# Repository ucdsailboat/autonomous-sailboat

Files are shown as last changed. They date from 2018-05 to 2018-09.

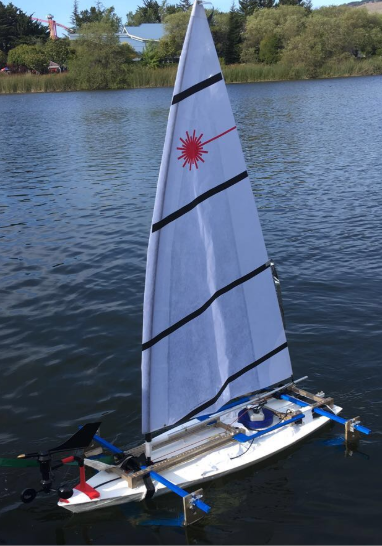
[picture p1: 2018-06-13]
Photos/sailboat.PNG

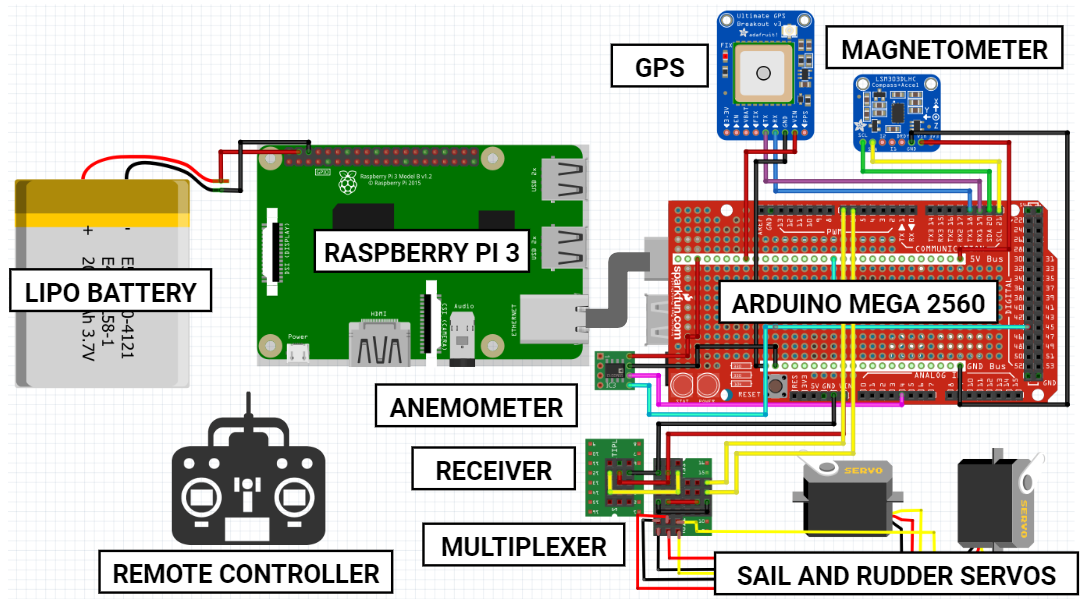
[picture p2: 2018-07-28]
Photos/fritzing sailboat.PNG

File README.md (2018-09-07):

# autonomous-sailboat
This is a repository for the Mechanical Engineering senior design project for UC Davis that focuses on developing an autonomous hydrofoil sailboat.

__Contributors:__ <br/>
Sean Blaevoet, <br/>
Jordan Leung, <br/>
Michele Shi, <br/>
Vivian Tran, <br/>
Bryan Zhao

__Special thanks to:__ <br/>
Davi Henrique & <br/>
University of Southampton Sailing Robot Team (https://github.com/Maritime-Robotics-Student-Society/sailing-robot)

__Robotic Sailboat Wiki at:__ <br/>
https://github.com/ucdsailboat/autonomous-sailboat/wiki

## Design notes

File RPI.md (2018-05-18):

RPI DOCUMENTATION
CONNECTING TO THE RPI WITH WINDOWS REMOTE DESKTOP CONNECTION
If you're setting up the RPI for the first time, you'll need to set it up for remote desktop connection by following this YouTube video and this blog link to fix the default cursor.

Otherwise, to use a laptop's mouse and keyboard, you'll need to connect to the RPi with Window's built-in Remote Desktop Connection (or equivalent on Linux or Mac).

Connect the RPi to the laptop with HDMI
Log into Window's remote desktop connection
COMPUTER: raspberrypi.local
USERNAME: pi
PASSWORD: eme185
DOWNLOADING ARDUINO LIBRARIES ON RPI
Zip folders of the libraries are in the repository.

Download and unzip the folders for the IMU, GPS, and ANEMOMETER. Make sure your .h and .cpp files are not in another folder or else the Arduino IDE won't find the library header.
Move folders to /usr/share/arduino/libraries/ with command terminal and type the following commands:
cd /home/pi/folderName
sudo mv folderName /usr/share/arduino/libraries/

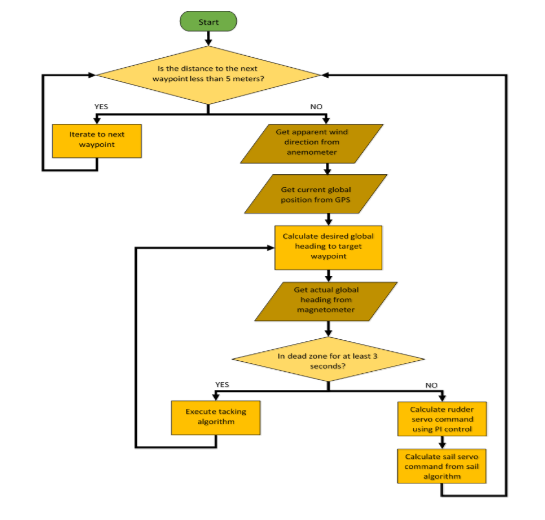
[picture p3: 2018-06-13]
Photos/waypoint tracking.PNG

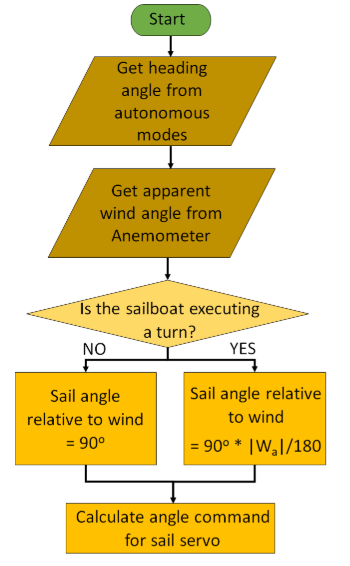
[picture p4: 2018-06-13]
Photos/sailcontroller.PNG

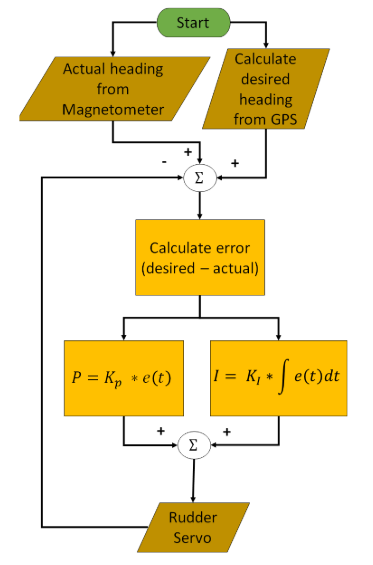
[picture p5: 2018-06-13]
Photos/ruddercontrol.PNG

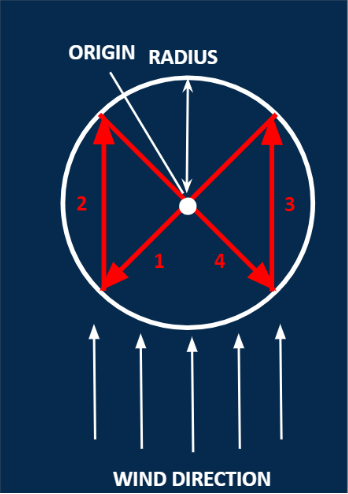
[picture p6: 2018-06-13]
Photos/WOphoto.PNG

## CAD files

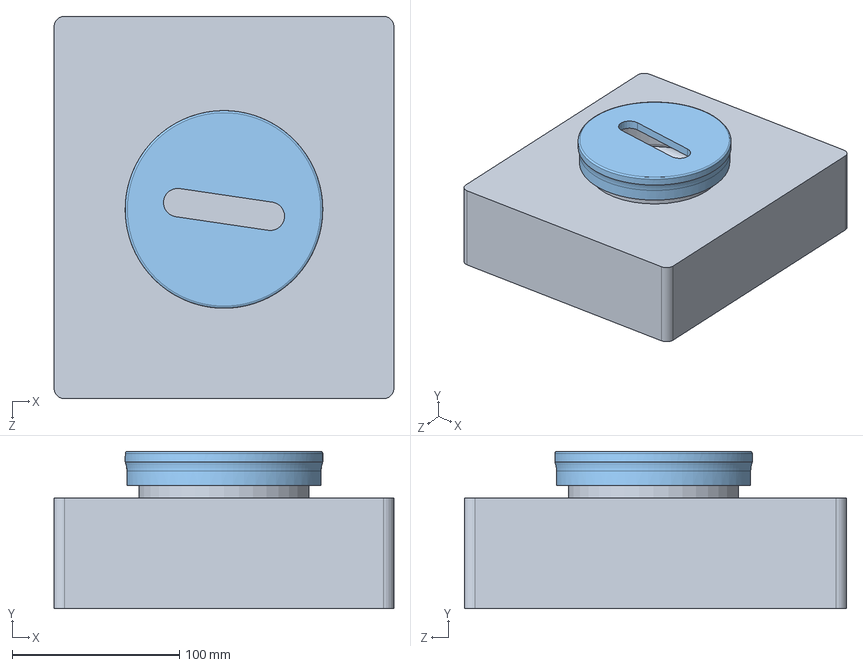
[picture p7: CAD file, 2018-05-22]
CAD/Model Sailboat external enclosure Assembly 5.18.18.SLDASM
203.2 x 94.0 x 228.6 mm
Model Sailboat internal enclosure
Enclosure O-Ring
External enclosure cap 5.18.18
External enclosure fitting 5.16.18

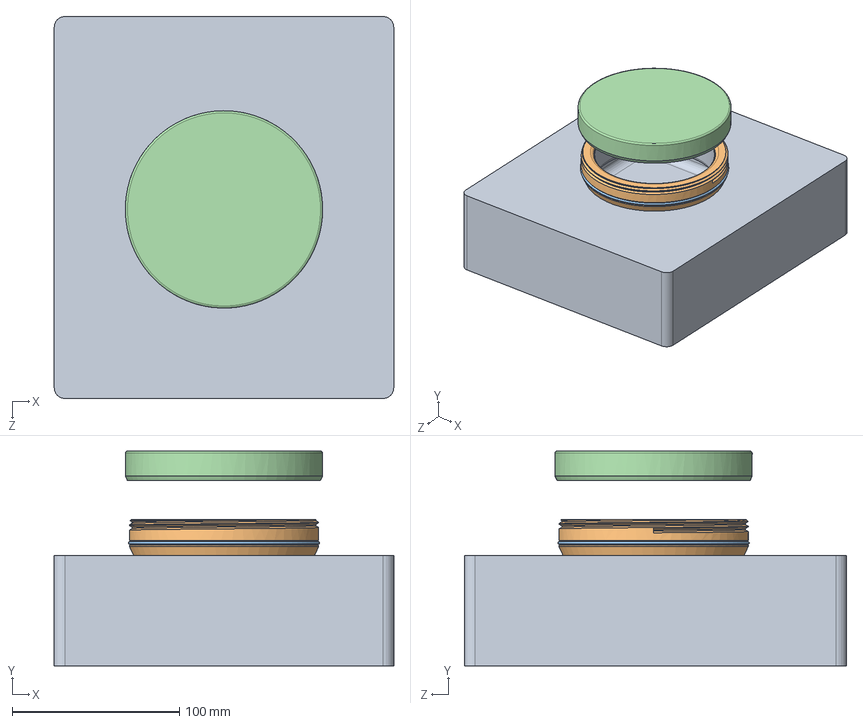
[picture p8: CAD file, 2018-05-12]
CAD/Model Sailboat external enclosure Assembly 5.11.18.SLDASM
203.2 x 128.7 x 228.6 mm
Model Sailboat internal enclosure
External enclosure fitting 5.11.18
Enclosure O-Ring
External enclosure cap 5.11.18

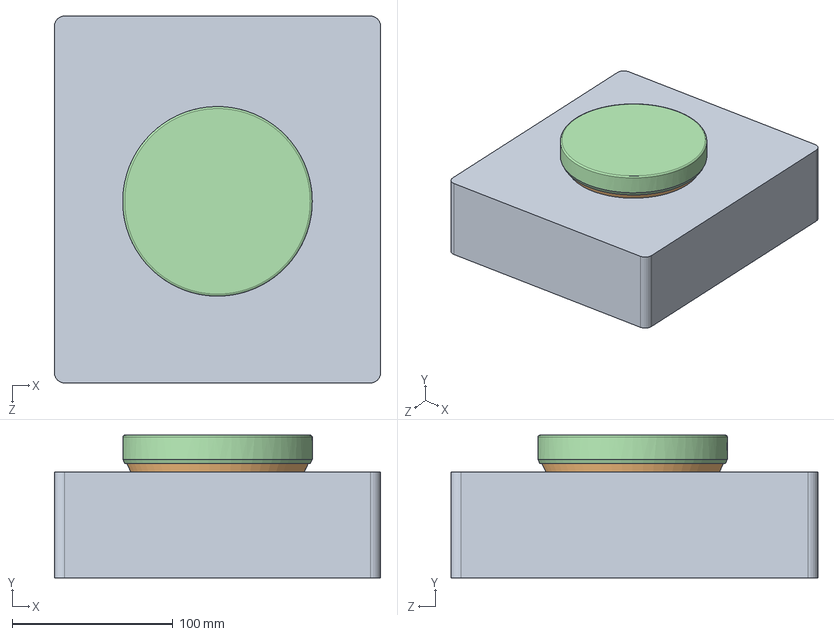
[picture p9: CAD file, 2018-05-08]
CAD/Model Sailboat external enclosure Assembly.SLDASM
203.2 x 88.9 x 228.6 mm
Model Sailboat internal enclosure
External enclosure fitting 5.2.18
Enclosure O-Ring
External enclosure cap 5.2.18

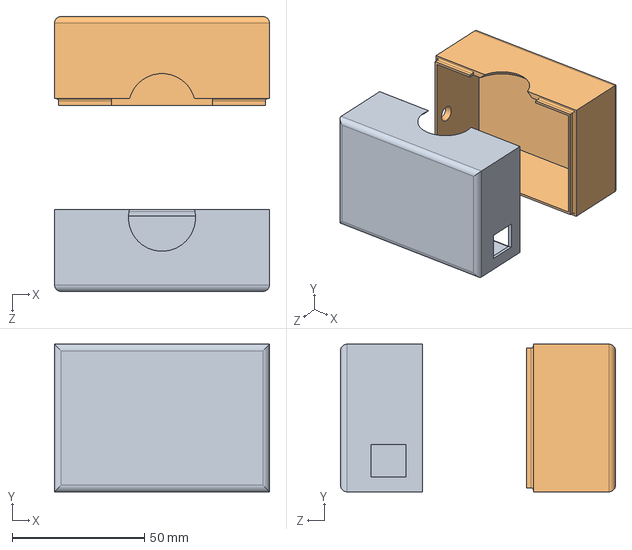
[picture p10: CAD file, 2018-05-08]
CAD/Joystick Assembly.SLDASM
81.3 x 55.9 x 104.0 mm
Joystick Left part
Joystick Right part

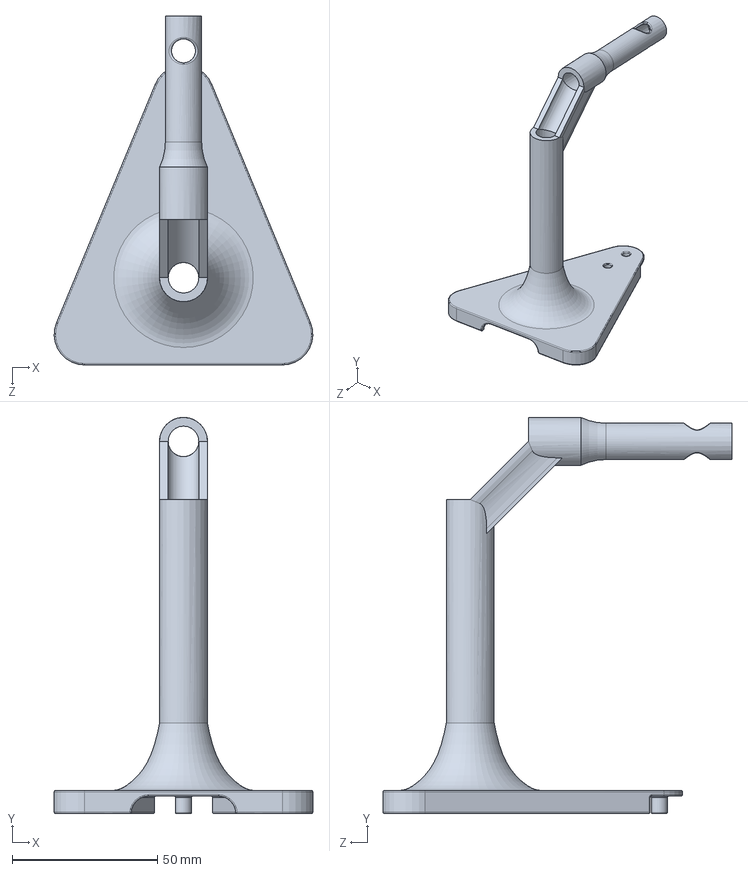
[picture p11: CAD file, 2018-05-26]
CAD/anemometer mount v1.6.SLDPRT
89.0 x 136.2 x 120.0 mm

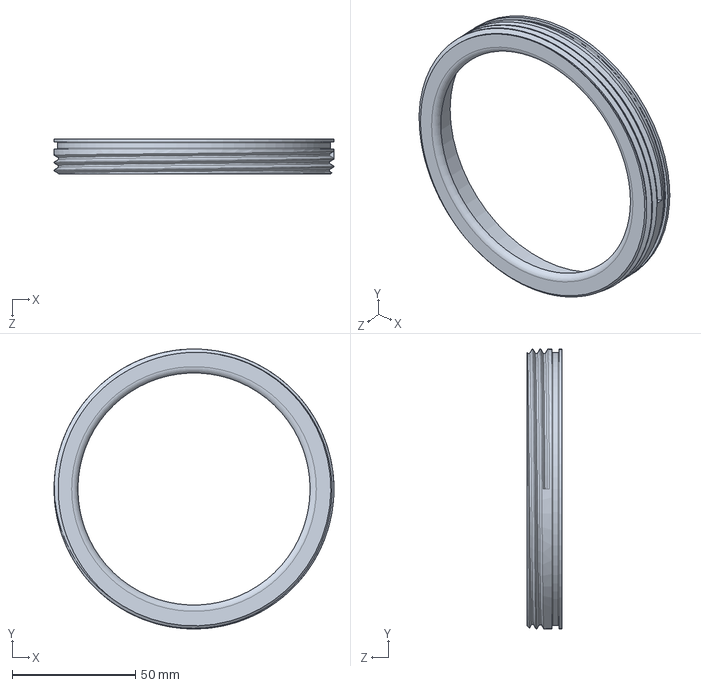
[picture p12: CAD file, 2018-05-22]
CAD/External enclosure fitting 5.16.18.SLDPRT
113.4 x 113.4 x 14.1 mm

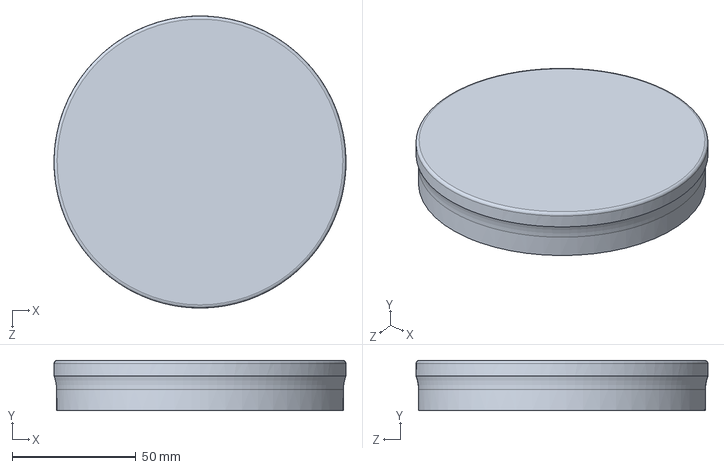
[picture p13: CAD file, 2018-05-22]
CAD/External enclosure cap 5.18.18.SLDPRT
118.1 x 20.3 x 118.1 mm

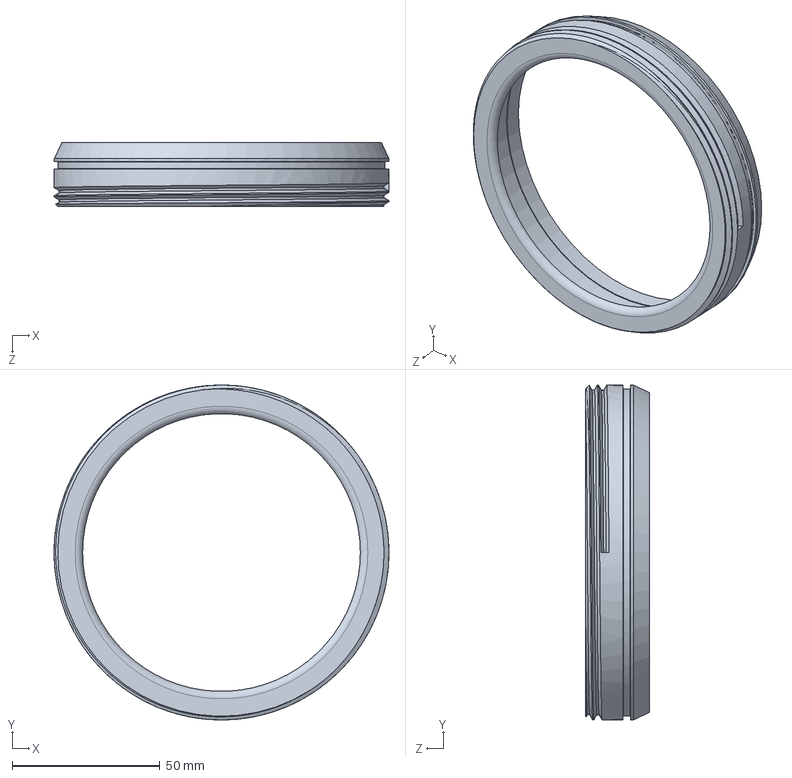
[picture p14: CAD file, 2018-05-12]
CAD/External enclosure fitting 5.11.18.SLDPRT
113.4 x 113.4 x 21.6 mm

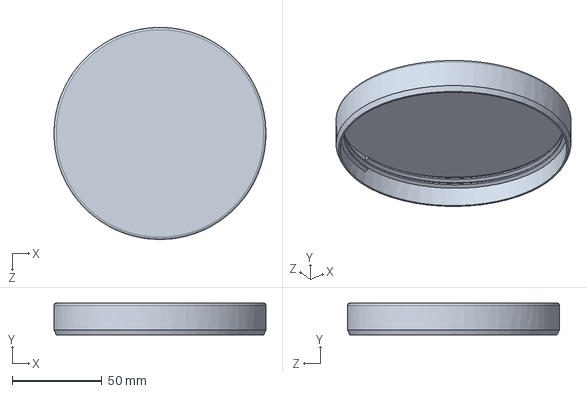
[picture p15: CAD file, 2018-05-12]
CAD/External enclosure cap 5.11.18.SLDPRT
118.1 x 17.8 x 118.1 mm

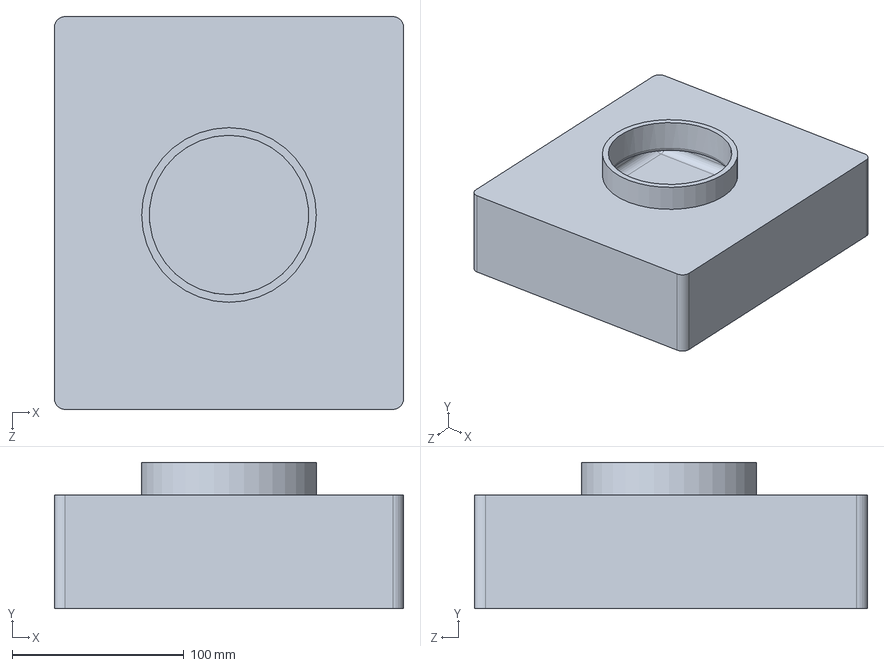
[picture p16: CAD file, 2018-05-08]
CAD/Model Sailboat internal enclosure.SLDPRT
203.2 x 85.1 x 228.6 mm

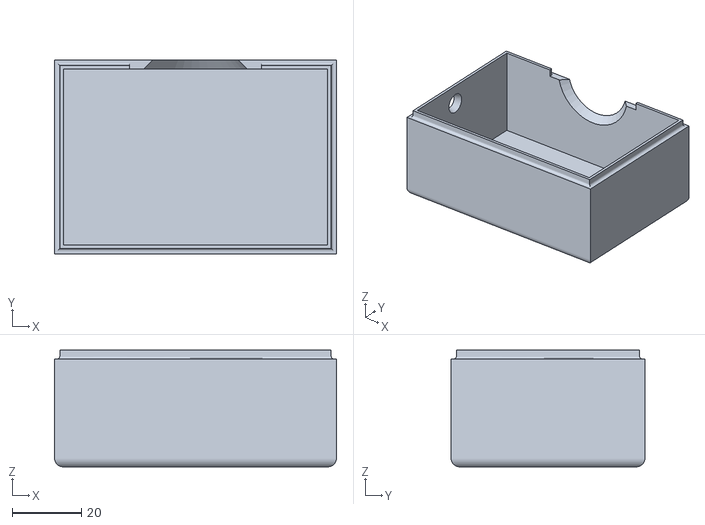
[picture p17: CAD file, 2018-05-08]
CAD/Joystick Right part rev1.STL
81.3 x 55.9 x 33.7

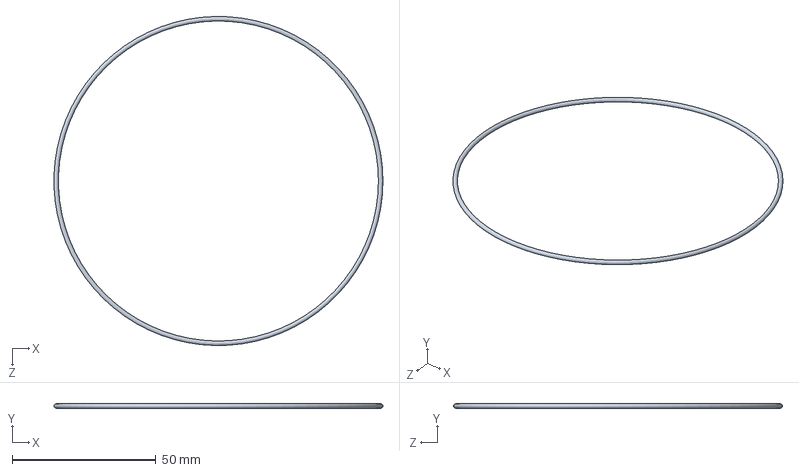
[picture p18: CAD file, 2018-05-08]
CAD/Enclosure O-Ring.SLDPRT
114.6 x 1.59 x 114.6 mm

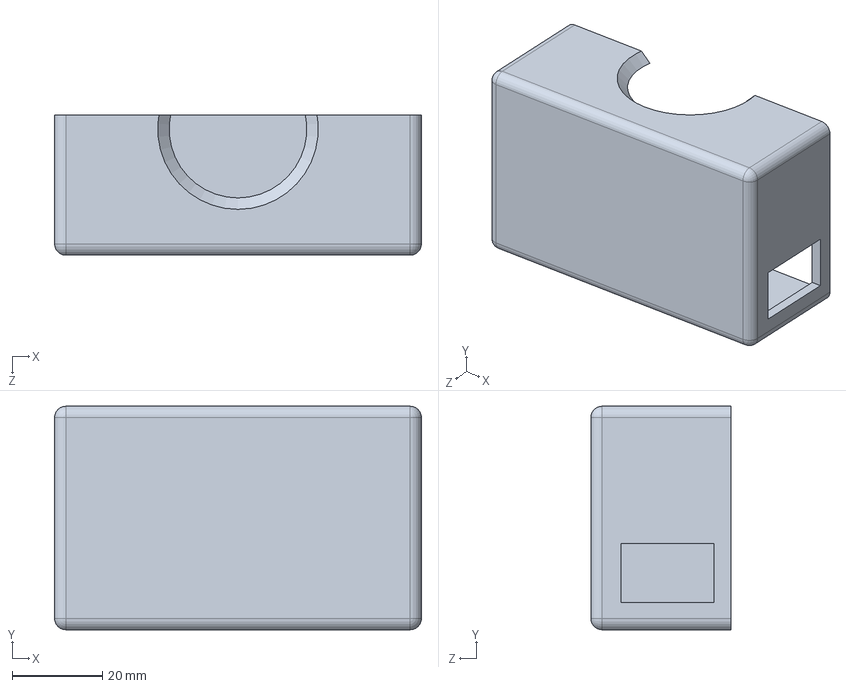
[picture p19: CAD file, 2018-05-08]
CAD/Joystick Left part.SLDPRT
81.3 x 49.5 x 31.1 mm

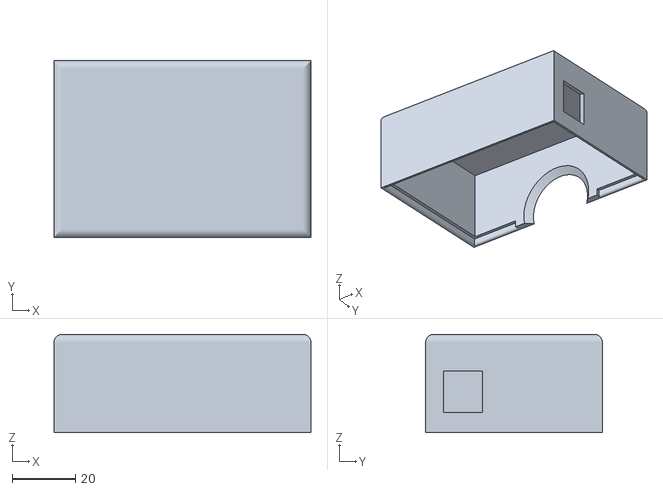
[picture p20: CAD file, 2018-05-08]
CAD/Joystick Left part rev1.STL
81.3 x 55.9 x 31.1

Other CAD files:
CAD/External enclosure cap 5.2.18.SLDPRT
CAD/External enclosure fitting 5.2.18.SLDPRT
CAD/Joystick Right part.SLDPRT
CAD/External enclosure fitting_Waterproof Test.SLDPRT
CAD/External enclosure cap 5.11.18.STL
CAD/External enclosure cap 5.18.18.STL
CAD/External enclosure cap 5.2.18.STL
CAD/External enclosure fitting 5.11.18.STL
CAD/External enclosure fitting 5.16.18.STL
CAD/External enclosure fitting 5.2.18.STL
CAD/External enclosure fitting_Waterproof Test.STL
CAD/anemometer mount v1.3.SLDPRT
CAD/anemometer mount v1.3.STL
CAD/anemometer mount v1.5.2.STL
CAD/anemometer mount v1.5.SLDPRT
CAD/anemometer mount v1.6.STL
CAD/anemometer mount.SLDPRT

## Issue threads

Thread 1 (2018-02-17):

Sample Issue

bryzhao, 2018-02-17:
You can notify people and let them know about different issues that you may have, e.g.

1. MATLAB script "example.m" doesn't execute properly because of line 34.
2. Jordan forgot how to write "hello, world" in Python.

You can make words **bold** and other words *italic* with Markdown formatting (edit comment to see formatting). You can also include different links like [this,](https://faculty.engineering.ucdavis.edu/sarigul/) Professor Sarigul-Klijn's page.

Closed 2019-05-08.

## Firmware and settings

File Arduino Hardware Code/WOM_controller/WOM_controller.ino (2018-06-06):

/*WIND OPTIMIZATION AUTONOMOUS MODE: This runs after the boat is set within the predefined radius (maxRadius) of the predefined origin (origin[2]). 
  While this is running, the sensor data will update every interval of "display_timer", with the anemometer wind speed updating every "T" seconds.
  It sends servo commands to the rudder and sail 
*/

//LIBRARIES
#include <math.h>  

// GPS libraries 
#include <TinyGPS++.h>
//#include <SoftwareSerial.h>

//Rudder libraries
#include <stdio.h>
#include <stdlib.h>

//Servo library
#include <Servo.h>

//Magnetometer
#include <Adafruit_LSM303_U.h>
#include <Adafruit_Sensor.h>
#include <Wire.h>

//VARIABLE INITIALIZATIONS
//Data Logging Initialization
float display_timer = 500;                //time (ms) between printing to the serial port

// Anemometer Initialization
#define WindSensorPin (2) 
int VaneValue;                            // raw analog value from wind vane
int CalDirection;                         // apparent wind direction: [0,180] cw, [0,-179] ccw, 180 is dead zone
float WindSpeed;                          // apparent wind speed (knots)
double T = 3.0;                           // time in seconds needed to average readings
unsigned long WindSpeedInterval = T*1000; // time in milliseconds needed to average anemometer readings 
unsigned long previousMillis = 0;         // millis() returns an unsigned long
volatile unsigned long RotationsCounter;  // cup rotation counter used in interrupt routine 
volatile unsigned long ContactBounceTime; // timer to avoid contact bounce in interrupt routine 
uint32_t timer = millis();

//GPS Initialization
TinyGPSPlus tinyGPS;        // Create a TinyGPS object
#define GPS_BAUD 9600       // GPS module baud rate
#define gpsPort Serial1

//Wind Optimization Initialization 
float origin[2] = {38.5629053, -121.7659831};   //GPS coordinates of origin (latitude, longitude) sequoia apt
//float origin[2] = {38.53876876, -121.72130584}; //Lake Spafford
float maxRadius = 14;          //m
float radius;               //current distance from origin
int againstWindAngle=180-45;  
float windAngle = 0;        //angle of wind in body frame (-180,180]
float desiredAngle =againstWindAngle;
boolean turning=0;          //turning flag because the boat is out of bounds
float previousMillisTurning;
float turningBuffer = 3000; // buffer to allow boat to turn and get back into boundary (ms)

//Rudder Initialization
int rOffset=103;
float rudderPos = 45+rOffset;      // positive rudder limit
float rudderNeg = -45+rOffset;     // negative rudder limit
float errorActual = 0;      // error = desired angle - actual angle 
float Iaccum = 0;           // accummulator of integrative error.
float Kp = 2;               // proportional gain - starting value suggested by Davi
float Ki = .001;               // integral gain - starting value suggsted by Davi
float controlAct = 0;      // initialize control action (P + I)
float heading=0;            // actual angle/direction
float angle_rudder = 0;     // angle of the rudder commanded 
float sample_time = 0.2;    // sample time of the system (in seconds)
int deg = 0;                // input angle into servo

Servo servoR;

//Sail Initialization 
int turnAngle = 45;               // turn angle in degrees to determine straight sailing or turns
int sDesired = 45;                 // desired sail angle to maintain relative to nose, uncalibrated  
int sZero = 60;                   // degrees required to zero sail servo in line with nose of boat
int sLimit = 90;                  // constraint angle limit to 90 degrees for the sail, determined by max slack allowed by rope length 
int sOffset=sZero - sDesired/12;  // calculated offset from getSailOffset necessary to map servo commands to sail angle (0 to 90 relative to boat nose) 
int sCommand;                     // calibrated angle command in degrees to servo.write 
int spSail;                       // set point sail angle relative to wind direction 
int currHeading = 0;                  // current heading relative to boat (0 to 180 clockwise, 0 to -179 counterclockwise)
int prevHeading = 0;                  // previous heading relative to boat 
Servo servoS;  

//Magnetometer Initialization
Adafruit_LSM303_Mag_Unified mag = Adafruit_LSM303_Mag_Unified(12345);
float previousTurnHeading;
float currTurnHeading;
float turnBufferAngle=10;
bool CW;
sensors_event_t magEvent;

//FUNCTION PROTOTYPES
// Anemometer Wind Direction Prototypes
int getWindDirection(int VaneValue);      

//GPS Prototypes
void printInfo(void);

//WO Prototypes
float haversin(float angle);


//Rudder Prototypes
float saturator(float value);
float saturator_rudder(float servoRudderAngle);
float rudder_controller(float desiredPath, float heading);
float P();
float I();

//Sail Prototypes
int getSailOffset(int sDesired);               // 0.85*sDesired + 60; used with getSailServoCommand
int getSailServoCommand(int sDesired);         // calibrate desired sail angle to angle command to servo.Write

//Magnetometer Prototypes
float gen_heading(float mag_x, float mag_y);


//SETUP 
void setup() {
  Serial.begin(9600); // min baud rate for GPS is 115200 so may have to adjust 
  
  // Anemometer Wind Direction Setup
  pinMode(WindSensorPin, INPUT); 
  
  // Anemometer Wind Speed Setup 
  attachInterrupt(0, isr_rotation, FALLING); 
  sei(); // Enables interrupts 
  
  //GPS Setup
  gpsPort.begin(GPS_BAUD); // GPS_BAUD currently set to 9600  

  //Rudder Setup
  servoR.attach(6);      // pin for the servoS control
  servoR.write(rOffset); // initialize at zero position 

  //Sail Setup
  servoS.attach(7);      // pin for the servoS control
  servoS.write(sZero); // initialize at zero position 
  
  //Magnetometer 
    if(!mag.begin())
  {
    /* There was a problem detecting the LSM303 ... check your connections */
    Serial.println("Oops, no LSM303 detected ... Check your wiring!");
    while(1);
  }

}





//LOOP 
void loop() {
  //[Update and Print Sensor Info]
  if (timer > millis())  timer = millis();                              //Reset timer if millis() or timer wraps around
  
  // Update wind speed
  if ((unsigned long)(millis()- previousMillis) >= WindSpeedInterval){  //Calculate wind speed after T seconds 
    // convert to knots using the formula V = P(2.25/T) / 1.15078 
    WindSpeed = RotationsCounter*2.25/T/1.15078;
    RotationsCounter = 0;                                               //Reset RotationsCounter after averaging  
    previousMillis = millis();
    }
    
  // Update wind direction
  VaneValue = analogRead(A4); 
  CalDirection = getWindDirection(VaneValue);
  
   
  if (CalDirection >= 174)                                              //Curve fit has values less than -179 
  CalDirection = 180; 
  if(CalDirection <= -172) 
  CalDirection = -179;                          
  
  //Print data to serial port
  if (millis() - timer > display_timer) {                               
    timer = millis();                                                   //Reset the timer    
    printInfo();                                                        //Print sensor data to serial port
  }
  smartDelay(50); // "Smart delay" looks for GPS data while the Arduino's not doing anything else




//[Wind Optimization] 
  windAngle = CalDirection;

  //Calculate radius from origin
  radius=tinyGPS.distanceBetween(origin[0],origin[1],tinyGPS.location.lat(),tinyGPS.location.lng());
  
  //If the boat is beyond maxRadius from the origin, determine which way to turn
  if (radius > maxRadius && !turning){  
    //Determine which way to turn                           
    if ( desiredAngle == againstWindAngle){      
      desiredAngle = 1;
      CW=1;                                 //CW turn to go with the wind
    }
    else if(desiredAngle == 1){
      desiredAngle = -againstWindAngle;
      CW=1;                                 //CW turn to go -45 against the wind
    }
    else if (desiredAngle == -againstWindAngle){
      desiredAngle = -1;
      CW=0;                                  //CCW turn to go with the wind
    }
    else if(desiredAngle == -1){
      desiredAngle = againstWindAngle;
      CW=0;                                 //CW turn to go 45 against the wind 
    }

    //Prep to turn                           
    previousMillisTurning=millis();
    turning=1;
    mag.getEvent(&magEvent);
    previousTurnHeading= gen_heading(magEvent.magnetic.x, magEvent.magnetic.y); // [-180, 180]
    }

   
//[Rudder Controller]
  //If the boat is turning, determine if the boat is still turning and/or out of bounds
  if (turning){ 
    mag.getEvent(&magEvent);
    currTurnHeading= gen_heading(magEvent.magnetic.x, magEvent.magnetic.y); // [-180, 180]
    
    if (CW && abs(previousTurnHeading-currTurnHeading)>(againstWindAngle+turnBufferAngle)) servoR.write(rudder_controller(previousTurnHeading+againstWindAngle+turnBufferAngle,currTurnHeading));         //Continue turning with the max rudder angle until the boat has turned around by at least againstWindAngle+turnBufferAngle (overshoots desiredAngle)
    else if (!CW && abs(previousTurnHeading-currTurnHeading)>(againstWindAngle+turnBufferAngle)) servoR.write(rudder_controller(previousTurnHeading-againstWindAngle-turnBufferAngle,currTurnHeading));
    else servoR.write(rudder_controller(desiredAngle, windAngle));
    if (radius<maxRadius)turning=0;     
  }
  else {
      servoR.write(rudder_controller(desiredAngle, windAngle));
  }

//[Sail Controller]  
  if ((abs(prevHeading - currHeading)) < turnAngle){           // if the trajectory turns the boat less than the turnAngle degrees, then maintain 90 degree relative sail angle
    spSail = 90;                                  // set point sail angle relative to wind direction
    sDesired = abs(abs(CalDirection) - spSail);   // CalDirection [-179,180], sail doesn't care about direction   
  }
  else {
    sDesired = sLimit*abs(CalDirection)/180;      // from Davi sail Control Law, executed on turns 
  }
  sCommand = getSailServoCommand(sDesired);       // calibrate desired sail angle to angle command for servo
  servoS.write(sCommand);                         // command sail servo
  prevHeading = currHeading;                              // current heading becomes previous heading 
  if (sCommand > 140)
  sCommand = 140;                                 // maximum for servo
  servoS.write(sCommand);                         // command sail servo
  prevHeading = currHeading;                      // current heading becomes previous heading 
  }




//FUNCTION DEFINITION
//Sensor Data Logging Function Definition
void printInfo(){
  /*
  //Print latitude (degs), longitude (degs), GPS speed (mph), wind direction (degs), wind speed (knots)
  Serial.print(tinyGPS.location.lat(), 8); Serial.print(","); 
  Serial.print(tinyGPS.location.lng(), 8); Serial.print(","); 
  Serial.print(tinyGPS.speed.mph()); Serial.print(",");
  Serial.print(CalDirection); Serial.print(","); 
  Serial.print(desiredAngle);Serial.print(",");
  Serial.println(WindSpeed); 
*/
  //for testing
  Serial.print(desiredAngle);Serial.print("\t");
  Serial.print(radius-maxRadius);Serial.print("\t");
  Serial.print(turning);Serial.print("\t");
  Serial.print(previousTurnHeading);Serial.print("\t");
  Serial.print(currTurnHeading);Serial.print("\t");
  Serial.print(currTurnHeading-previousTurnHeading);Serial.print("\t");
  Serial.print(abs(previousTurnHeading-currTurnHeading)>(againstWindAngle+turnBufferAngle));Serial.print("\t");
  Serial.print(CW);Serial.print("\t");
  Serial.print(errorActual);Serial.println("\t");
}



//WO Function Definition
float haversin(float angle){                //radians
    return pow(sin(angle/2),2);
}


   
// Anemometer Function Definition
// Interrupt function to increment the rotation count 
void isr_rotation () { 
  if ((millis() - ContactBounceTime) > 15 ) {     // Debounce the switch contact.
    RotationsCounter++; 
    ContactBounceTime = millis(); 
  }
}
int getWindDirection(int VaneValue){              // Potentiometer values mapped to [-179,180], curve fit from data
  return 0.3387*VaneValue - 172.4; ;  
}



// GPS Function Definition
static void smartDelay(unsigned long ms){
  // This custom version of delay() ensures that the tinyGPS object is being "fed". From the TinyGPS++ examples.
  unsigned long start = millis();
  do{
    // If data has come in from the GPS module
    while (gpsPort.available())
      tinyGPS.encode(gpsPort.read());           // Translate from NMEA format
  } while (millis() - start < ms);
}



//Rudder Controller Definitions
float saturator(float value) {
  //Maps [0-360] to [-180,180]
  if (value > 180)  value = value - 360;
  if (value < -180) value = value + 360;
  return value;
}
float saturator_rudder(float servoRudderAngle) {
  //Keeps rudder angle within limits
  if (servoRudderAngle > rudderPos) servoRudderAngle = rudderPos;
  if (servoRudderAngle < rudderNeg) servoRudderAngle = rudderNeg;
  return servoRudderAngle;
}
float rudder_controller(float desiredPath, float heading) {
  desiredPath = saturator(desiredPath);           //same as desired angle
  errorActual = desiredPath - heading;            //error between the actual heading and desired path
  errorActual = saturator(errorActual);
  controlAct = P() + I();                        //PI control
  angle_rudder = saturator_rudder(rOffset + (rudderNeg-rOffset)*controlAct/180);
  return angle_rudder;
}
float P(){
  return Kp * errorActual;
}
float I() {                                         //error is reduced at each iteration                                 
  Iaccum = Iaccum + Ki * errorActual * sample_time;
  return Iaccum;
}



//Sail Controller Definitions
int getSailOffset(int sDesired){            // used in getSailServoCommand function 
  return sDesired*0.85 + sZero;             // curve fit of data 
}
int getSailServoCommand(int sDesired){
  if(sDesired >= sLimit) {  // for desired sail angles greater than the limit, return the limit
    sCommand = getSailOffset(sLimit);
    return round(sCommand);
    }
  else {                    // for all other sail angles, return the calibrated sail angle 
    sCommand = getSailOffset(sDesired);
    return round(sCommand); 
    }
}


//Magnetometer
// generates current heading in global coordinates from magnetometer values
float gen_heading(float mag_x, float mag_y){
  // convert Gauss units (microteslas) to current compass heading, without tilt compensation
  float currHeading = (atan2(mag_y,mag_x) * 180) / PI; //
  // map the heading so that north is at 0, and the heading goes clockwise
  if (currHeading < -180)
  {
    currHeading = 360 + currHeading;
  }

  // remap to [-180, 180] for the boat heading
  if (currHeading > 180){
    currHeading = currHeading - 360;
  }
  else {
    // keep the currHeading the same, since it's between 0 and 180
  }
  return currHeading;
} // end of function

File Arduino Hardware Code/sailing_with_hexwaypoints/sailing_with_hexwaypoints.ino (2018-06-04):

/* Sail and Rudder Controls
Description: Incorporated sailing with 6 waypoints in a hexagonal shape at the Sac Aquatic Center. 
The rudder controller is responsible for adjusting the boat orientation
with respect to the defined trajectory. The directions of the compass and the desired path 
are compared. The sail controller optimizes the length of the rope to control the sail based on
the incoming wind angle relative to the boat.

Inputs: desiredPath - angle that the bsailboat needs to travel to reach the waypoint
    heading - actual direction (angle) found via compass
Outputs: angle_rudder - angle of the rudder (type float)

Connections: 
 *  Anemometer: A4 for Wind Direction, Pin 2 for Wind Speed
 *  Sail Servo: Signal to Pin 7
 *  Rudder Servo: Signal to Pin 6
 *  Magnetometer: SDA to SDA, SCL to SCL, Power to Vin, GND to GND
 *  GPS: TX1 to 18, RX1 to 19
Updated by: Jordan Leung, Bryan Zhao, Michele Shi 5/25/18
*/

// rudder controller libraries
#include <StandardCplusplus.h>
// #include <serstream>
// #include <string>
#include <vector> // for waypoints

//#include <iterator>
//#include <stdio.h>
//#include <stdlib.h>
#include <Servo.h>
#include <math.h>
#include <Wire.h>
//#include <TinyGPS++.h>
#include <Adafruit_Sensor.h>
#include <Adafruit_LSM303_U.h>
#include <TinyGPS.h>

// definitions
//#define PI 3.14159265 // (replace with M_PI)
#define RX 4 // on the arduino pins
#define TX 3
#define gpsPort Serial1
#define BAUDRATE 9600

// data logging initialization
float display_timer = 500; // time (ms) rate to print to the serial port 

// anemometer wind direction 
#define WindSensorPin (2) // pin location of the anemometer sensor 
int VaneValue;            // raw analog value from wind vane
int CalDirection;         // apparent wind direction: [0,180] CW, [0,-179] CCW, 180 is dead zone

// rudder ctrl 
TinyGPS gps; // gps object
Servo servoRudder; // declare a servo object
float distMargin = 4.0; // margin of error for waypoints (defined as a radius in [meters]) 
// SoftwareSerial ss(TX, RX); // use pins 4 and 3 for SW serial ports
//using hardware serial 
//HardwareSerial mySerial = Serial1;

// anemometer wind speed
float WindSpeed;                          // apparent wind speed in knots 
double T = 3.0;                           // time in seconds needed to average readings
unsigned long WindSpeedInterval = T*1000; // time in milliseconds needed to average anemometer readings 
unsigned long previousMillis = 0;         // millis() returns an unsigned long
volatile unsigned long RotationsCounter;  // cup rotation counter used in interrupt routine 
volatile unsigned long ContactBounceTime; // timer to avoid contact bounce in interrupt routine 
uint32_t timer = millis(); 

// Sail Servo Init
Servo servoS;                    // servo object for sail servo 
int turnAngle = 45;              // turn angle in degrees to determine straight sailing or turns
int sDesired = 0;                // desired sail angle relative to nose, uncalibrated  
int sZero = 60;                  // degrees required to zero sail servo in line with nose of boat
int sLimit = 90;                 // constraint angle limit to 90 degrees for the sail, determined by max slack allowed by rope length 
int sOffset;                     // calculated offset from getSailOffset necessary to map servo commands to sail angle (0 to 90 relative to boat nose) 
int sCommand;                    // calibrated angle command in degrees to servo.write 
int spSail;                      // set point sail angle relative to wind direction 

// Anemometer Wind Direction Prototyping
int getWindDirection(int VaneValue);           // anemometer requires calibration using curve fit data

// Sail Servo Prototyping
int getSailOffset(int sDesired);               // 0.85*sDesired + 60; used with getSailServoCommand
int getSailServoCommand(int sDesired);         // calibrate desired sail angle to angle command to servo.Write

// assign a unique ID to this sensor at the same time
Adafruit_LSM303_Mag_Unified mag = Adafruit_LSM303_Mag_Unified(12345);

int point;
/* Rudder Controller Init */
// 103 - starting value for the rudder orientation on the sailboat
int rudOffset = 103;      //offset to zero position (parallel with nose)
// define rudder negative and positive limits 
float rudderPos = 45 + rudOffset; // degrees
float rudderNeg = -45 + rudOffset; // degrees 
float rudderAngle = 0.0; // output angle for the rudder servo
//approximate time of code execution
float sampleTime = 0.2; // sample time of the system (in seconds)
//initialize PID variables
float errorActual = 0; // error = desired angle - actual angle 
float Iaccum = 0;    // accummulator of integrative error.
float Kp = 2;           // proportional gain - starting value suggested by Davi
float Ki = 0.001;       // integral gain - starting value suggsted by Davi
// 0 - north, 90 - east, 180/-180 - south, -90 - west 
// desired path/direction
float desiredPath;
float currHeading;  // current actual angle/direction in degrees
float prevHeading; // store previous heading

// data storage variables
float velocity; // abs. vel of boat [km/h -> NEEDS TO BE CHANGED]
float direction; // current course angle (heading of boat)

// GPS holds positional data
struct location {
  float latitude;
  float longitude;
};

// rudder controls with waypoint navigation
location currentLocation, targetLocation; // define structs with gps coordinates
float distanceWP = 20.0; // holds value of the distance between waypoints, start it at higher value
bool reached = false; // flag for printing if waypoint is reached 
std::vector<location> hexWaypoints; // vector that holds all the different waypoints 
int iterWP = 0; // iterator for waypoints vector

std::vector<location> triWaypoints; // for testing at lake spafford
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

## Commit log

2018-03-04 Add files via upload
    The Arduino Library for the IMU and the Adafruit Unified Sensor Driver. Links to guides can be found under the screening chart.
2018-03-04 Add files via upload
    The modified sensorapi Arduino code for the BNO055 IMU. The current outputs are Euler angles, linear acceleration, magnetic strength, and calibration status.
2018-04-23 Starting PI controller for rudder based on Davi controllers
2018-04-28 Add files via upload
    Updated Servo Code with better optimization for Sail servo (myservob)
2018-04-28 Rudder fixed to -45 to 45 degree rotation
    [Analog_Joystick_w_Rudder_Servo.ino]
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2018-04-30 updated with hole for sensor mount
    [anemometer mount.SLDPRT, anemometer mount.STL]
2018-04-30 reduced sensor mounting hole distance from the end of the pipe
    [anemometer mount.SLDPRT, anemometer mount.STL]
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2018-05-02 updated cad
    [anemometer mount.SLDPRT]
2018-05-03 Add files via upload
    added function for heading (without tilt compensation), and copied over example code for calibration status
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2018-05-11 Anemometer Speed using millis() and preliminary sail control
2018-05-12 Add files via upload
    Updated dimensions of fitting inner diameter (smaller) and cap inner diameter (smaller)
    Updated geometry of anemometer to accommodate front spool and dimensions of bore size for mounting anemometer
    [External enclosure cap 5.11.18.SLDPRT, External enclosure cap 5.11.18.STL, External enclosure fitting 5.11.18.SLDPRT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]
2018-05-12 List of hexagon waypoints in setup()
    point 1 begins in lower left corner, point 6 ends at lower right corner; look at attached image ("google_earth_points") for leg lengths of hexagon
2018-05-14 Outputs string of Wind Direction, Wind Speed (Knots), LAT, LON, Boat Speed (Knots)
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2018-05-18 Rename Arduino Hardware Code/2_joystick_with_servo_and_xbee.ino to Arduino Hardware Code/Archive/2_joystick_with_servo_and_xbee.ino
2018-05-18 Rename Arduino Hardware Code/Analog_Joystick.ino to Arduino Hardware Code/Archive/Analog_Joystick.ino
2018-05-18 Rename Arduino Hardware Code/Analog_Joystick_w_Rudder_Servo.ino to Arduino Hardware Code/Archive/Analog_Joystick_w_Rudder_Servo.ino
2018-05-18 Rename Arduino Hardware Code/Analog_Joystick_w_Sail_Servo.ino to Arduino Hardware Code/Archive/Analog_Joystick_w_Sail_Servo.ino
2018-05-18 Rename Arduino Hardware Code/GPS_IMU.ino to Arduino Hardware Code/Archive/GPS_IMU.ino
2018-05-18 Rename Arduino Hardware Code/IMU.ino to Arduino Hardware Code/Archive/IMU.ino
2018-05-18 Rename Arduino Hardware Code/IMU_XBEE.ino to Arduino Hardware Code/Archive/IMU_XBEE.ino
2018-05-18 Rename Arduino Hardware Code/XBEE.ino to Arduino Hardware Code/Archive/XBEE.ino
2018-05-18 Rename Arduino Hardware Code/Servos_Xbees_and_Joysticks.ino to Arduino Hardware Code/Archive/Servos_Xbees_and_Joysticks.ino
2018-05-18 Rename Arduino Hardware Code/joysticks_and_xbee.ino to Arduino Hardware Code/Archive/joysticks_and_xbee.ino
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2018-05-26 Add files via upload
    Fixed thickening rod extrusion that would prevent anemometer wire from feeding under mount.
    [anemometer mount v1.6.SLDPRT, anemometer mount v1.6.STL]
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2018-05-26 Calibration functions fixed
2018-05-26 sail limit, sail var, and bracket fix
    debugging
    [WO_controller.ino]
2018-05-26 rudder direction works correctly&added sail limits
    [integrated_sail_rudder_v2.ino]
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2018-05-30 Update sailing_with_hexwaypoints.ino
    added 4th waypoint (origin) and set 45 rudder angle after it hits it
2018-06-02 Update tacking.cpp
    added saturation to ensure that the rudderangle does not pass 45 degrees
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2018-06-02 Testing with professors, 3 waypoints
    [boatTracker_hex_6-2-18.csv]
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2018-06-04 Rename Arduino Hardware Code/Rudder Controller updated.cpp to Arduino Hardware Code/Archive/Rudder Controller updated.cpp
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2018-06-13 Rename boatTracker 05-20-2018.csv to boatTracker_05-20-2018.csv
    [boatTracker_05-20-2018.csv]
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2018-06-14 Rename Data Logs/boatTracker 05-14-2018.csv to Data Logs/csv/boatTracker 05-14-2018.csv
    [boatTracker 05-14-2018.csv]
2018-06-14 Rename Data Logs/boatTracker 05-20-2018.csv to Data Logs/csv/boatTracker 05-20-2018.csv
    [boatTracker 05-20-2018.csv]
2018-06-14 Rename Data Logs/boatTracker._tackingcsv to Data Logs/csv/boatTracker_tacking.csv
    [boatTracker_tacking.csv]
2018-06-14 Rename Data Logs/boatTracker_05-20-2018.csv to Data Logs/csv/boatTracker_05-20-2018.csv
    [boatTracker_05-20-2018.csv]
2018-06-14 Rename Data Logs/boatTracker_WO1.csv to Data Logs/csv/boatTracker_WO1.csv
    [boatTracker_WO1.csv]
2018-06-14 Rename Data Logs/boatTracker_hex2.csv to Data Logs/csv/boatTracker_hex2.csv
    [boatTracker_hex2.csv]
2018-06-14 Rename Data Logs/boatTracker_hex_6-2-18.csv to Data Logs/csv/boatTracker_hex_6-2-18.csv
    [boatTracker_hex_6-2-18.csv]
2018-06-14 Rename Data Logs/boatTracker_memorial_morn.csv to Data Logs/csv/boatTracker_memorial_morn.csv
    [boatTracker_memorial_morn.csv]
2018-06-14 Rename Data Logs/boatTracker_working_hex.csv to Data Logs/csv/boatTracker_working_hex.csv
    [boatTracker_working_hex.csv]
2018-06-14 Rename Data Logs/boatTracker_working_hex_2.csv to Data Logs/csv/boatTracker_working_hex_2.csv
    [boatTracker_working_hex_2.csv]
2018-06-14 Rename Data Logs/boatTrackerhex2.csv to Data Logs/csv/boatTrackerhex2.csv
    [boatTrackerhex2.csv]
2018-06-14 Deleted original and reuploaded same file
    [boatTracker_hex.csv, boatTrackerhex.csv]
